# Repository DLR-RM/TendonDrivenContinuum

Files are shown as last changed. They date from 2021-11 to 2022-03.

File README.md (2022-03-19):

# Open Source Tendon-Driven Continuum Mechanism: A Platform for Common Research in Soft Robotics 

<p align="center">
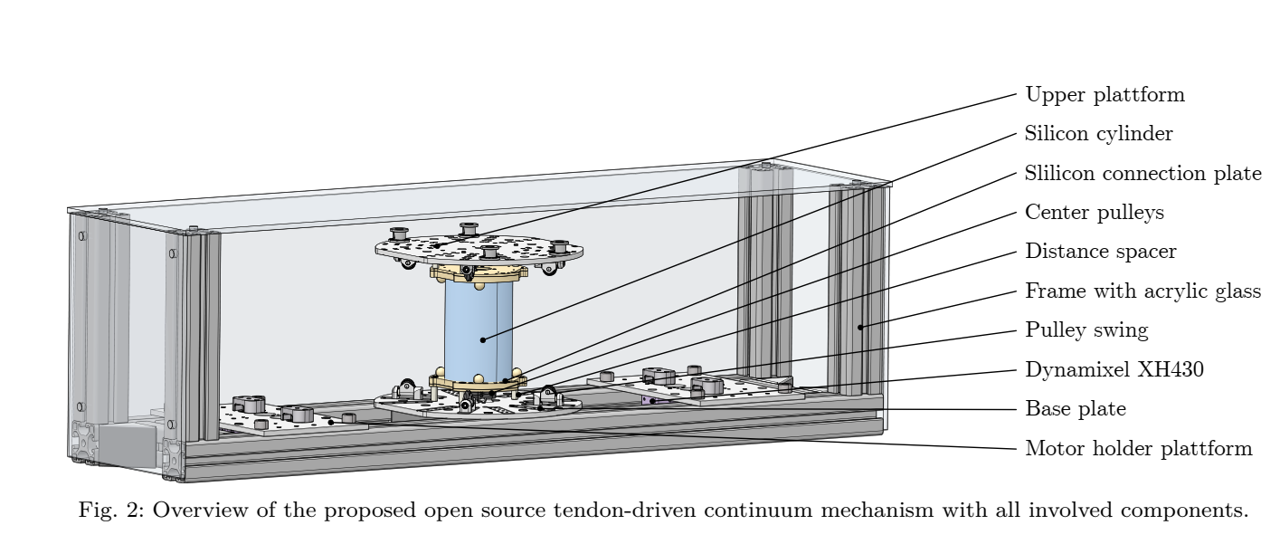
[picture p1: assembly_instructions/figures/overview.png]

</p>

This repository covers the CAD files (.stp) and assembly instruction to built a tendon-driven continuum mechanism research platform. If you want to built this system, please reference our corresponding publication [1].

## Abstract of the publication [1]
This paper introduces a tendon-driven continuum mechanism platform for research on design, modeling, state estimation, and control of this challenging robotic component envisioned as highly versatile and mechanically robust joint for future robotic systems. To propel the corresponding research areas, a common platform is presented for benchmarking and transferability of results, approaches, and designs among different research groups. The proposed mechanical design including all components is open source, whereas electronics and actuation are off-the-shelf. Research groups are enabled to build up their own system as all relevant CAD-files and assembly instructions are made accessible through GitHub. With that, a fundamental goal in research is achieved and will push continuum joints towards real application scenarios for future soft robots.

## Content of the repository

| Description | Link | Subfolder
| --- | --- | --- |
| Creo Design | [tdc_neck_asm.stp](https://github.com/DLR-RM/TendonDrivenContinuum/blob/main/CAD/tdc_neck_asm.stp) | [CAD](https://github.com/DLR-RM/TendonDrivenContinuum/tree/main/CAD) |
| Assembly Instructions |[Assembly Instructions Overview](https://github.com/DLR-RM/TendonDrivenContinuum/blob/main/assembly_instructions/assembly_instructions_overview.pdf).| [Assembly Instructions](https://github.com/DLR-RM/TendonDrivenContinuum/tree/main/assembly_instructions) |
| Control Interface | | 
| Readable Version | [deutschmann2022_robosoft_final_submission.pdf](https://github.com/DLR-RM/TendonDrivenContinuum/blob/main/paper/deutschmann2022_robosoft_final_submission.pdf) |[paper](https://github.com/DLR-RM/TendonDrivenContinuum/tree/main/paper) |

[1] Deutschmann, Bastian, Reinecke, Jens, Dietrich, Alexander: "Open Source Tendon-driven Continuum Mechanism: A common Platform for Research in Soft Robotics" accepted for publication in: IEEE International Conference on Soft Robotics (Robosoft), 2022.

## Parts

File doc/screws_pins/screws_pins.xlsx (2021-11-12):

Screws:
Type | diameter [mm] | length [mm] | amount | factor of testbed | Total | for which junction?
Cylinderhead | M3 | 8 | 4 | 2 | 8 | BPOM to BPOU
Cylinderhead | M2 | 6 | 6 | 2 | 12 | BPOO to BPOU
Cylinderhead | M4 | 25 | 3 | 2 | 6 | interface plate through distance spacer to lower/upper platform
Cylinderhead | M2 | 4 (8) | 4 | n_t*2 | n_t*8 | pulley swing to lower/upper platform (pulley swing through distance plate to lower/upper platform)
Cylinderhead | M3 | 8 | 6 | 1 | 6 | one side of the silicon mold to the other
Cylinderhead | M3 | 12 | 12 | 1 | 6 | connet assembled mold to interface upper/lower plates
Cylinderhead | M2 | 6 | 1 | n_t | n_t | connect Dynamixel interface plate with Dynamixel
Cylinderhead | M2.5 | 12 | 4 | n_t | n_t*4 | connect Dynamixel with motor holder plate
Cylinderhead | M2 | 4 | 4 | n_t | n_t*4 | connect Dynamixel interface plate with winch
Dowel pins:
Type | diameter | length | amount | factor of testbed | Total | for which junction?
H | 4 | 8 | 2 | 2 | 4 | BPOO to BPOU
H | 4 | 7 | 1 | n_t*2 | n_t*2 | pulley to swing

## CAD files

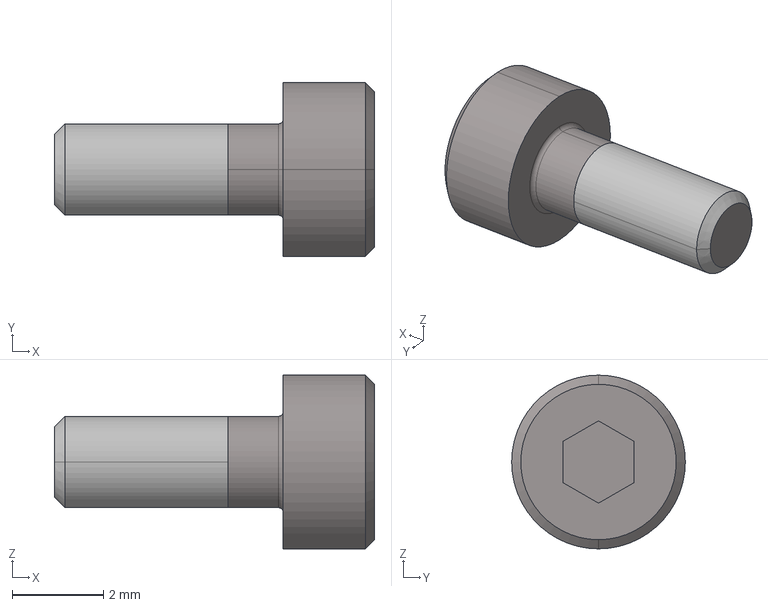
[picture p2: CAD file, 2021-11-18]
CAD/sc_d912_m02x05_af44_prt.stp
7.00 x 3.80 x 3.80 mm

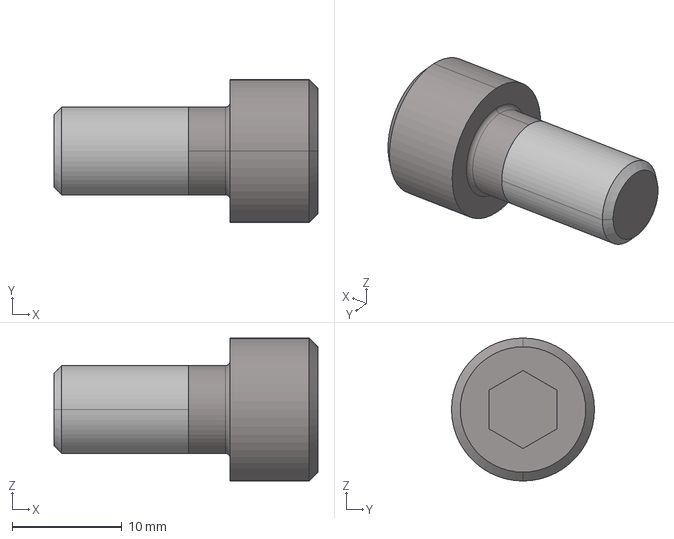
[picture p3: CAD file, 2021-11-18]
CAD/sc_d912_m08x16_prt.stp
24.0 x 13.0 x 13.0 mm

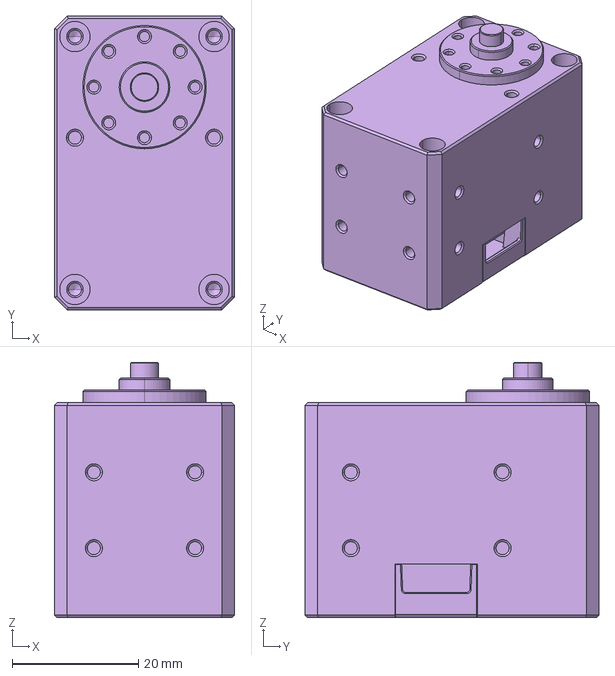
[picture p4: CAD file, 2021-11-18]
CAD/x-430_idle_prt.stp
28.5 x 46.5 x 40.4 mm

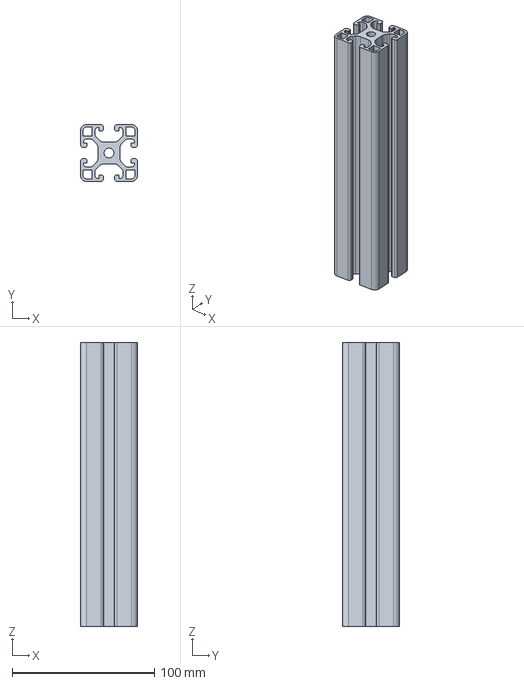
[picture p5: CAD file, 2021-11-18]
CAD/kt_item8_40x40_l_af26_prt.stp
40.0 x 40.0 x 200.0 mm

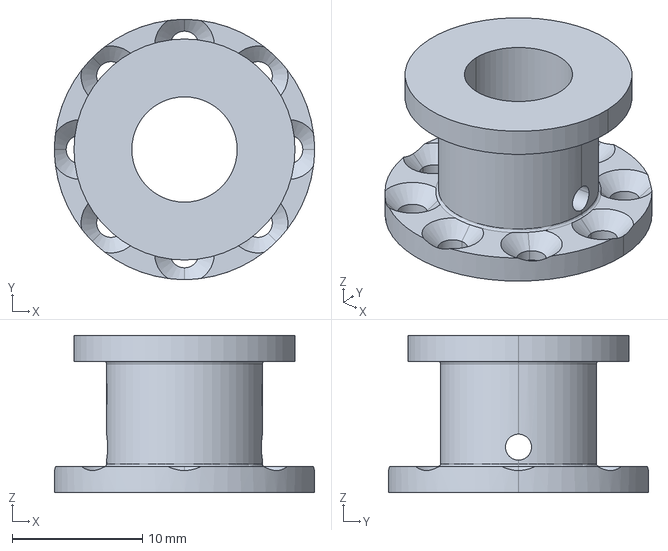
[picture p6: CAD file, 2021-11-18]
CAD/tdc_simpl_elast_winch_prt.stp
20.0 x 20.0 x 12.1 mm

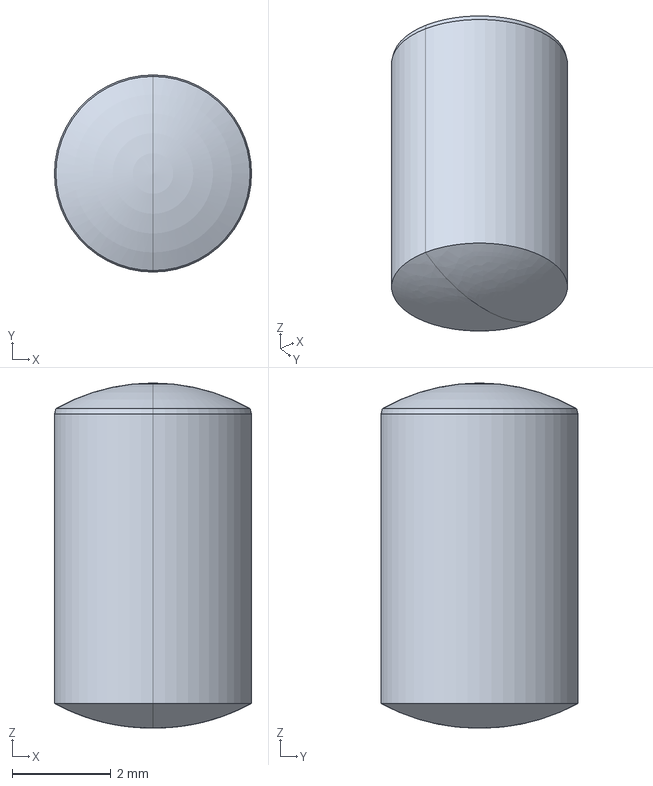
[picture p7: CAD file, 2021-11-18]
CAD/ps_d6325_04x07_prt.stp
4.00 x 4.00 x 7.00 mm

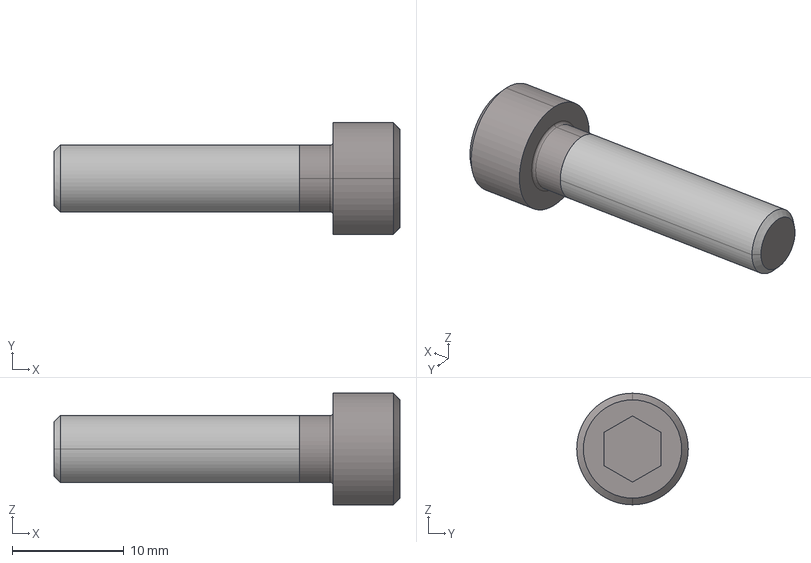
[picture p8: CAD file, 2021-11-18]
CAD/sc_d912_m06x25_af9_prt.stp
31.0 x 10.0 x 10.0 mm

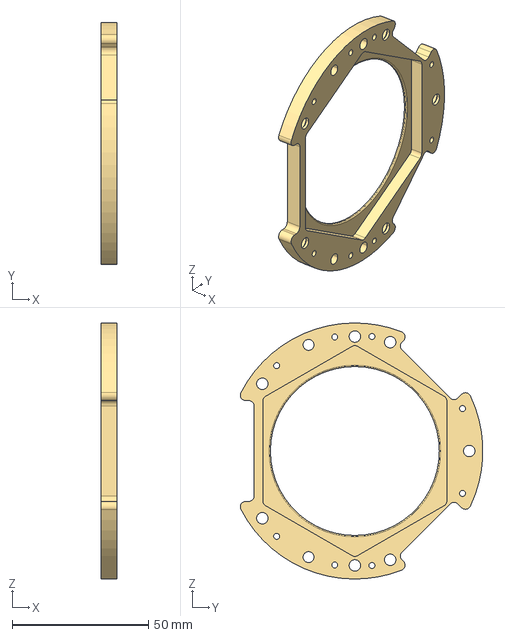
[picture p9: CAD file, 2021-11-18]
CAD/tdc_neck_bpoo_prt.stp
5.70 x 89.0 x 94.0 mm

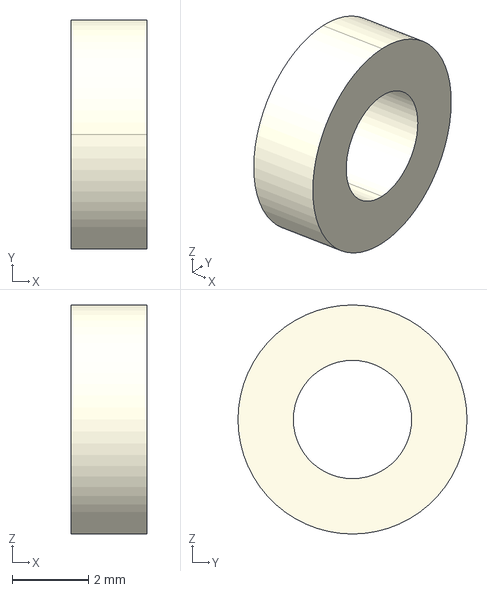
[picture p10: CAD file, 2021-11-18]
CAD/kt_distanzhuelse_03-06_af20_prt.stp
2.00 x 6.00 x 6.00 mm

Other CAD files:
CAD/sc_d912_m02x05_af45_prt.stp
CAD/sc_d912_m02x05_af49_prt.stp
CAD/sc_d912_m02x05_af53_prt.stp
CAD/sc_d912_m02x05_af42_prt.stp
CAD/sc_d912_m02x05_af46_prt.stp
CAD/sc_d912_m02x05_af38_prt.stp
CAD/sc_d912_m02x05_af63_prt.stp
CAD/sc_d912_m02x05_af43_prt.stp
CAD/sc_d912_m02x05_af37_prt.stp
CAD/kt_distanzhuelse_03-06_af17_prt.stp
CAD/kt_distanzhuelse_03-06_af18_prt.stp
CAD/kt_distanzhuelse_03-06_af19_prt.stp
CAD/kt_distanzhuelse_03-06_af21_prt.stp
CAD/kt_distanzhuelse_03-06_af22_prt.stp
CAD/kt_distanzhuelse_03-06_af23_prt.stp
CAD/kt_distanzhuelse_03-06_af24_prt.stp
CAD/kt_distanzhuelse_04-06_af12_prt.stp
CAD/kt_distanzhuelse_04-06_af13_prt.stp
CAD/kt_distanzhuelse_04-06_af14_prt.stp
CAD/kt_distanzhuelse_04-06_af15_prt.stp
CAD/kt_distanzhuelse_04-06_af16_prt.stp
CAD/kt_distanzhuelse_04-06_af17_prt.stp
CAD/kt_item8_40x40_l_af18_prt.stp
CAD/kt_item8_40x40_l_af19_prt.stp
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

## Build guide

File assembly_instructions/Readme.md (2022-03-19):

# Content 
The order of assembly is detailed in [Assembly Instructions Overview](https://github.com/DLR-RM/TendonDrivenContinuum/blob/main/assembly_instructions/assembly_instructions_overview.pdf).

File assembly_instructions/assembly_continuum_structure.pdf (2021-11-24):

## Assembly instructions: continuum structure

Bastian Deutschmann, Jens Reinecke and Alexander Dietrich

{Bastian.Deutschmann, Jens.Reinecke, Alexander.Dietrich}@dlr.de

DLR.de • slide 1

## Overview testbed

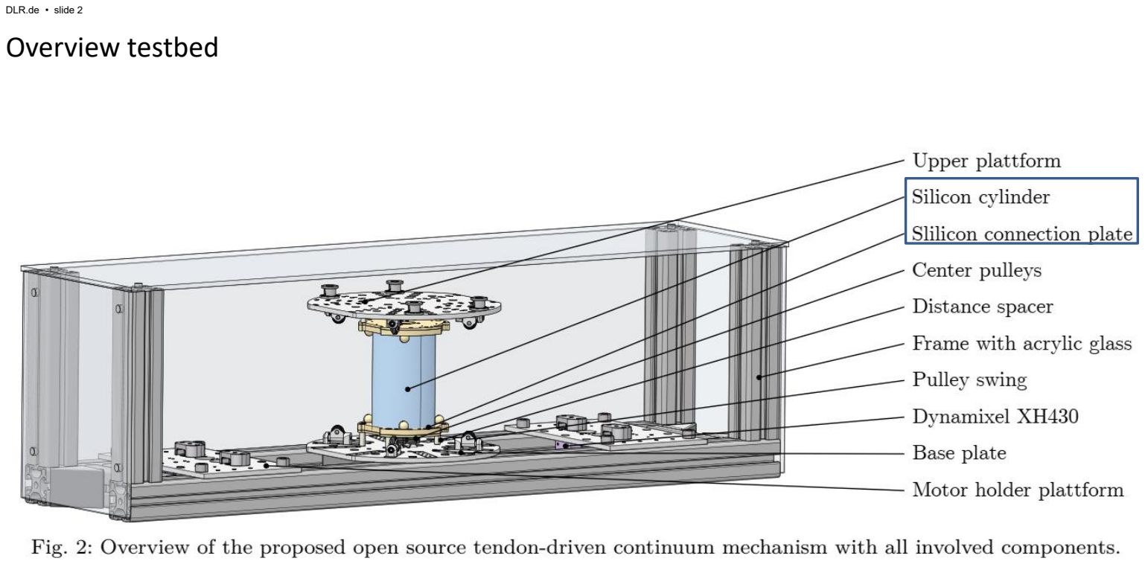
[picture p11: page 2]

## Overview of the contiuum structure

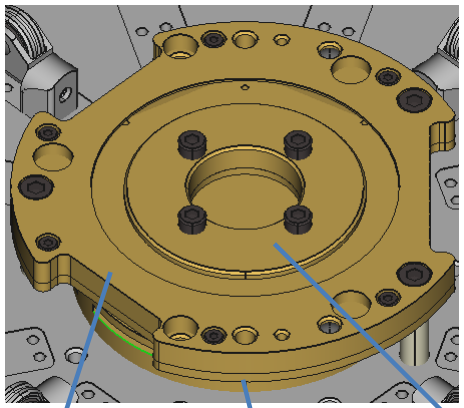
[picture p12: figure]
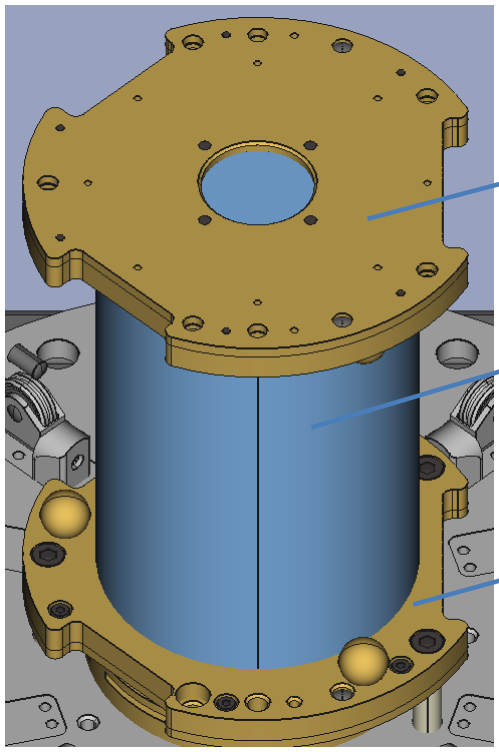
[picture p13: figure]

Upper interface plate

Lower interface plate

Continuum structure

TDC_NECK_BPOU

TDC_NECK_BPOO | TDC_NECK_BPOM

## Continuum structure components

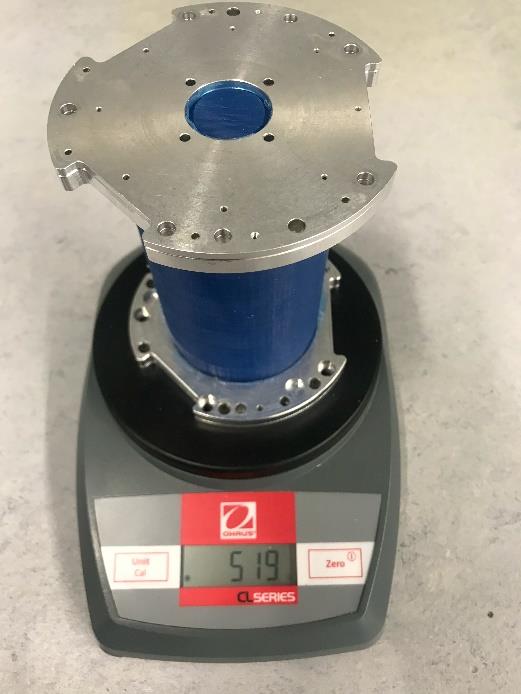
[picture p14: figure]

Manufacturing parts:
- Interface plate (3 parts)
- Lower part interface plate (TDC_NECK_BPOU)
- upper part interface plate (TDC_NECK_BPOO)
- Middle part interface plate (TDC_NECK_BPOM)
- Molds (3D-printed)
- Funnel (3D-printed)

Off-the-shelf parts:
- 2x2x dowel pin h6 ø4x8
- 2x6x Cylinderhead screw M2x6
- 2x4x Cylinderhead screw M3x8
- 6x Cylinderhead screw M3x8mm
- Silicon (e.g. Dragon skin shore 30A)
- Release Agent

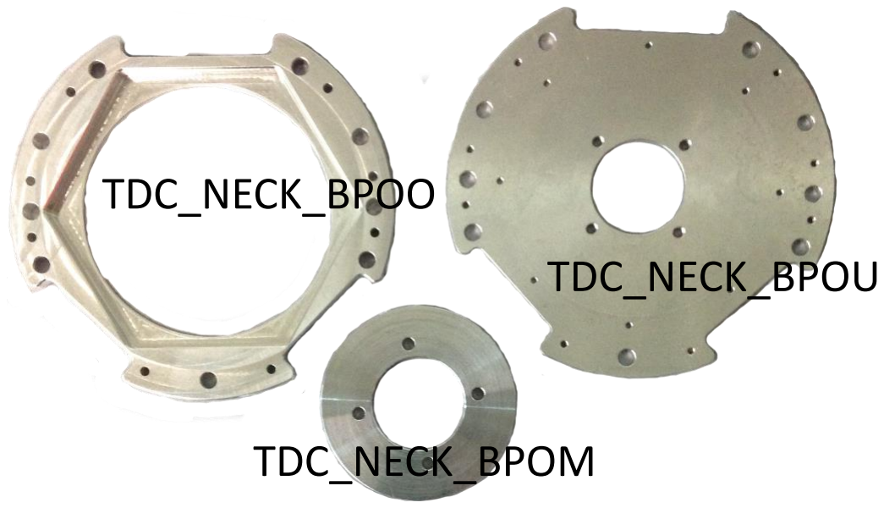
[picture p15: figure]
TDC_NECK_BPOU; TDC_NECK_BPOO; TDC_NECK_BPOM

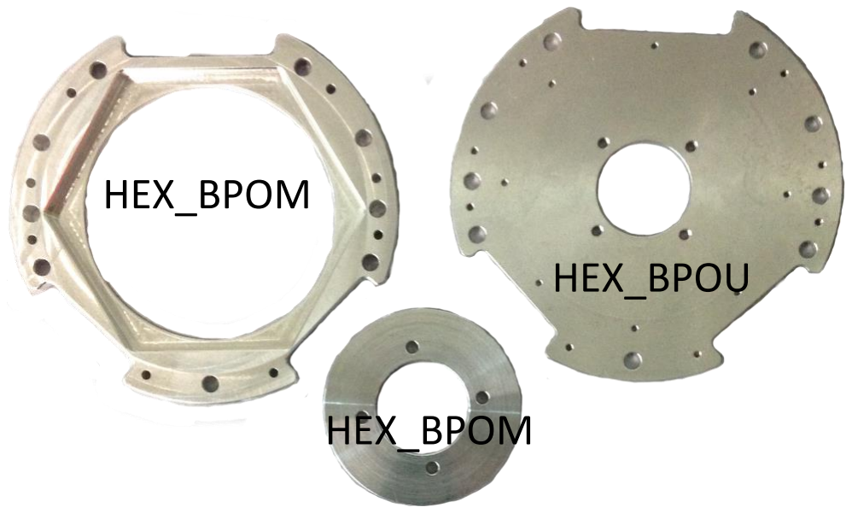
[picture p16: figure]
HEX_BPOU; HEX_BPOM

## Assembly interface plate

Tools:
- Allenkey
- Parallel plyers

Instructions:
- Clean all parts using iso-propanol
- Pair HEX_BPOO and HEX_BPOU by the dowel pins using the parallel plyers
- Pair HEX_BPOO and HEX_BPOU with 6x M2x6 using an allenkey
- Pair HEX_BPOU and HEX_BPOM with 4x M3x8 using an allenkey
- Repeat all steps for 2nd interface plate

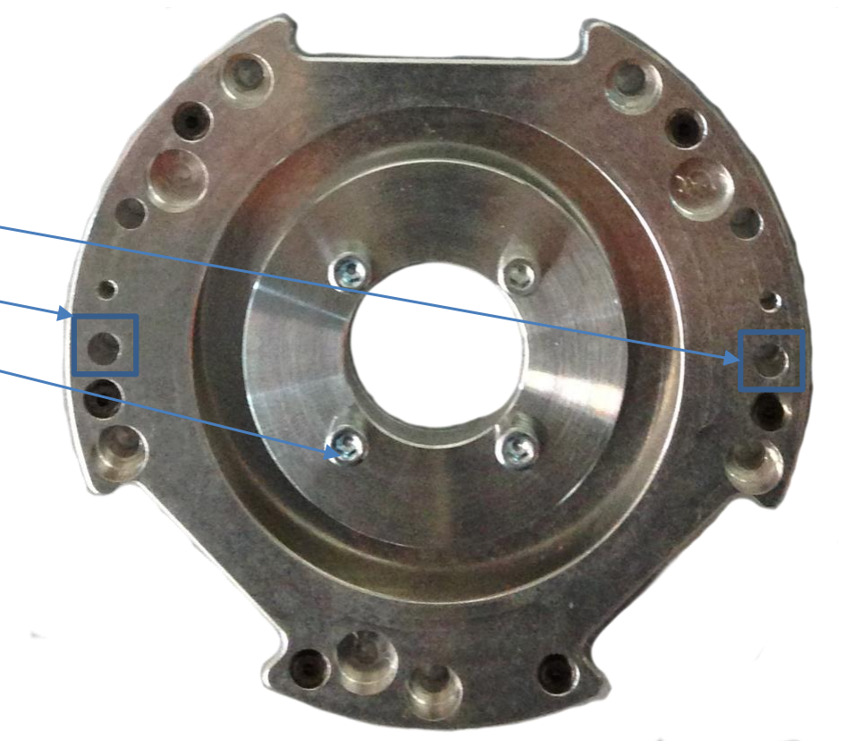
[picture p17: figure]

## Assembly of interface plate and moldings

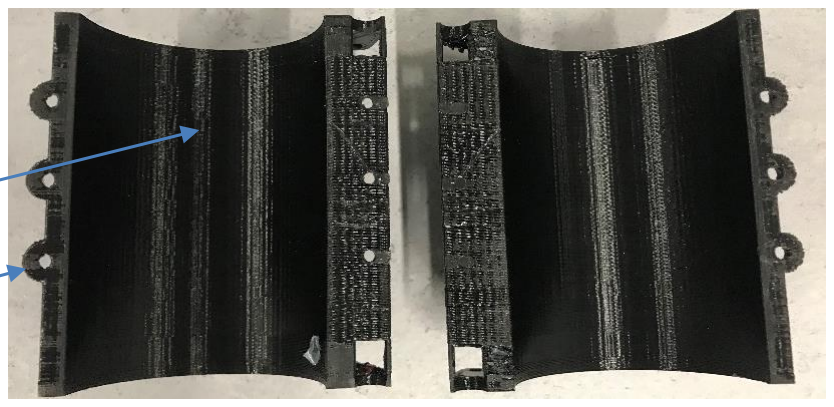
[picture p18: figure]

Tools:
- Allenkey

Instructions:
- Cover the inside of the molds with the release agent
- Pair the two molds with each other using 6x M3x8 and corresponding nuts
- Pair the molds and the lower and upper interface plate using screws 2x6x M2x12

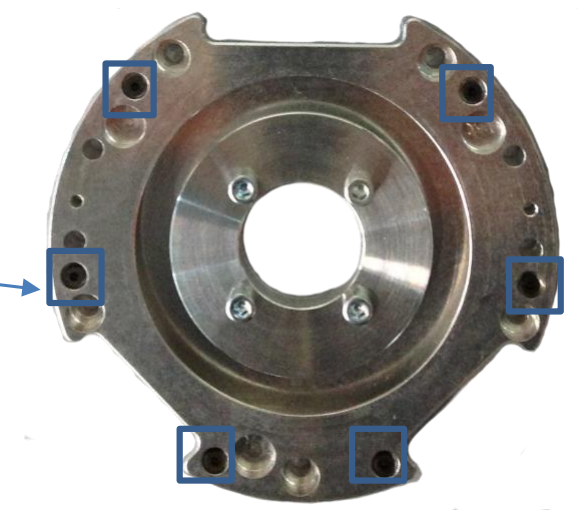
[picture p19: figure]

## Instructions for moldings

Tools
- Vacuum pump
- Container for to mix 2-component silicon & Stirring staff
- Digital scale

Parts:
- Assembled interface plates with moldings
- 3D-printed Funnel

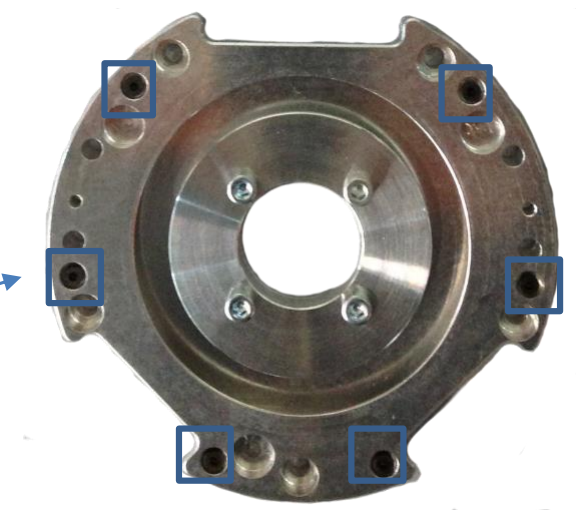
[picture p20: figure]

Instructions
- Mix 2 component silicon in container at the correct ratio (using the scale) with the stirring staff.
- Evacuate the mixture by a vacuum pump to remove air-bubbles with the mixture
- Pure the evacuated mixture into the assembled moldings using the funnel
- Let it cure for the respective time (24h for dragon skin)
- Remove the molds
- Pair HEX_BPOO and HEX_BPOU with 2x 6x M2x6 using an allenkey

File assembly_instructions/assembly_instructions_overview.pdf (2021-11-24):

## Assembly instructions: overview

Bastian Deutschmann, Jens Reinecke and Alexander Dietrich

{Bastian.Deutschmann, Jens.Reinecke, Alexander.Dietrich}@dlr.de

DLR.de • slide 1

## Overview testbed

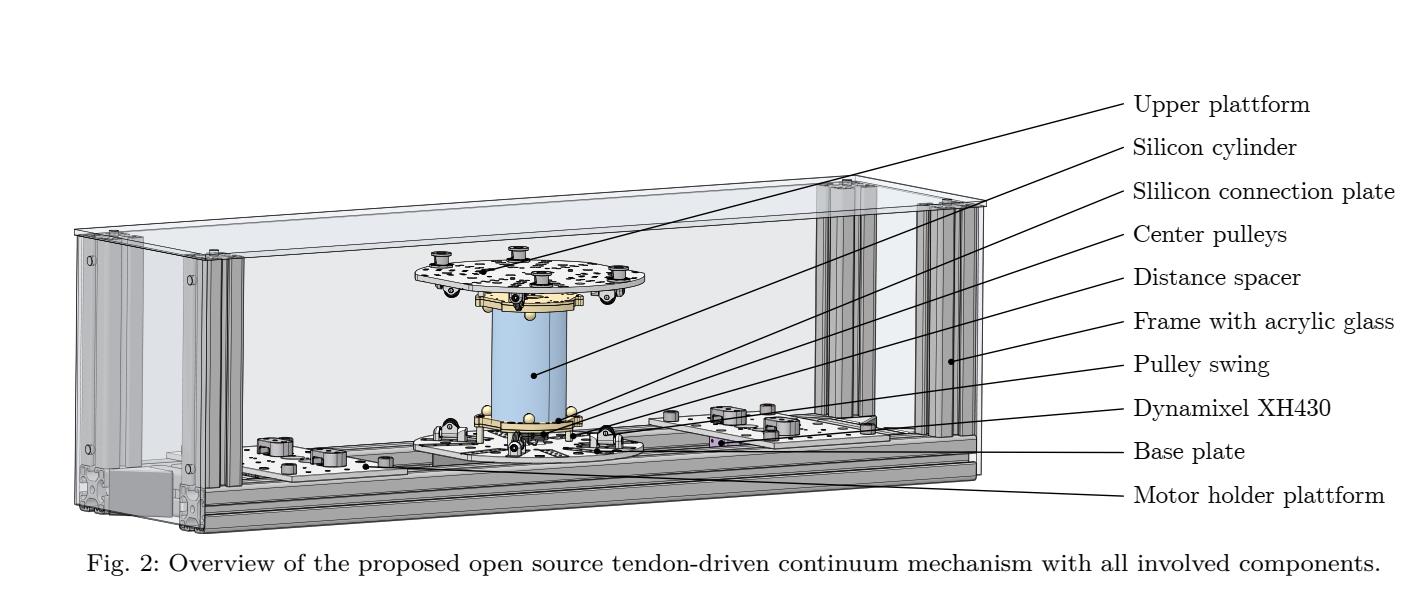
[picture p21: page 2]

## Assembly instructions: overview

In order to assemble the open source testbed, the following order of assembly is suggested:

1) Assembly of pulley swing
2) Assembly of continuum structure (Silicon cylinder)
3) Assembly of continuum and platform
4) Assembly of tendons
5) Assembly of motor holder platform

In order to perform each of the five steps, please refer to the corresponding assembly instruction .pdf file

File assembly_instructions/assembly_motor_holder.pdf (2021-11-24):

## Assembly instructions: motor holder

Bastian Deutschmann, Jens Reinecke and Alexander Dietrich

{Bastian.Deutschmann, Jens.Reinecke, Alexander.Dietrich}@dlr.de

DLR.de • slide 1

## Overview testbed

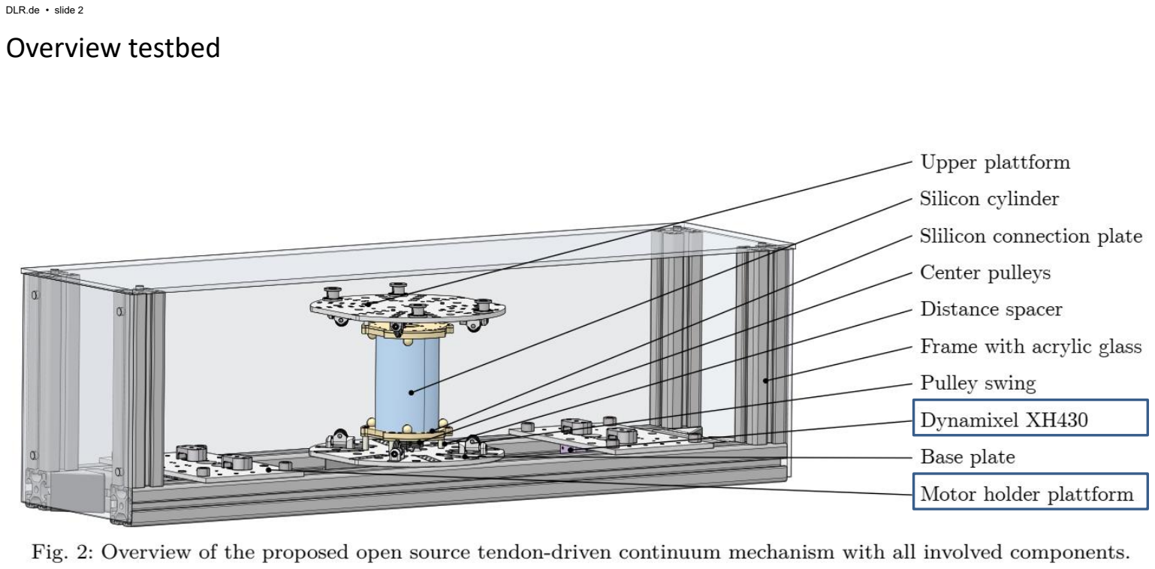
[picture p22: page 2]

## Overview of motor holder

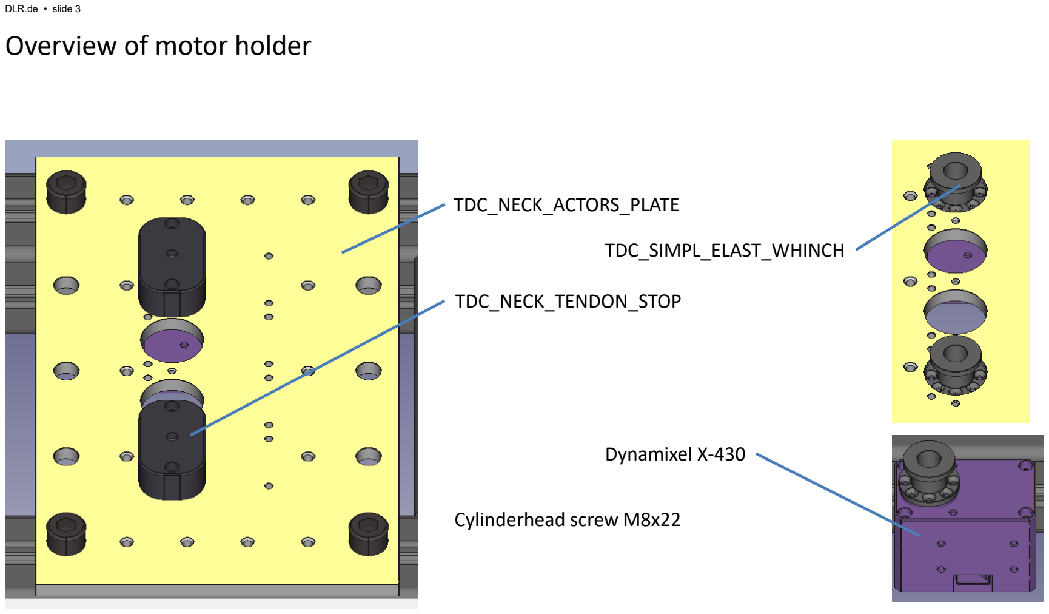
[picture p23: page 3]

TDC_NECK_ACTORS_PLATE

TDC_NECK_TENDON_STOP

Cylinderhead screw M8x22

TDC_SIMPL_ELAST_WHINCH

Dynamixel X-430

## Components

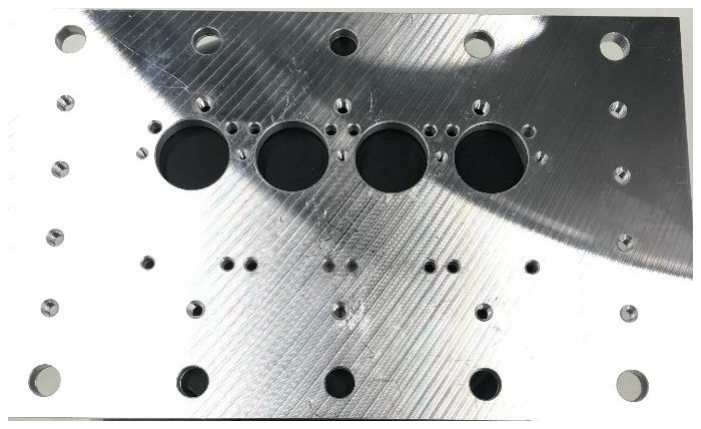
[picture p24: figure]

Manufacturing parts
- 2x motor holder plater (TDC_NECK_ACTORS_PLATE )
- n_t tendon winches (TDC_SIMPL_ELAST_WINCH)
- N_t Tendon stops (TDC_NECK_TENDON_STOP)

Off-the-shelf parts:
- n_t Dynamixel motors with interface plate
- 4xn_tx M2.5x12 (mount Dynamixel on holder)
- 4xn_tx M2x4 (mount winch on Dynamixel interface plate)
- n_tx M2x6 (mount interface plate on Dynamixel output shaft

Tools:
- Allenkey

## Assembly instructions: motor holder

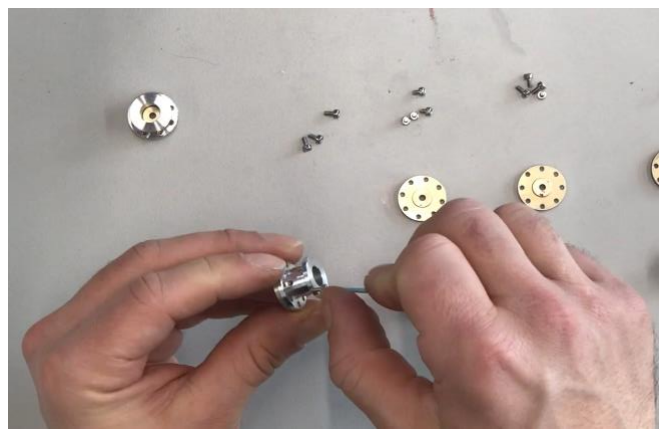
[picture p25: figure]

Instructions:
- Mount each of the n_t winches onto the Dynamixel interface plate using 4xM2x4 cylinderhead screws
- Connect each Dynamixel interface plate with the output shaft of a dynamixel motor using M2x6 cylinderhead screw
- Mount each of the n_t dynamixel motor with 4xM2.5x12 cylinderhead screw to the actuator plate
- Mount each of the n_t tendon stops onto the motor holder plate

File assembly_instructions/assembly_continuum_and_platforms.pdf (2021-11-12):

## Assembly instructions: continuum structure and the platforms

Bastian Deutschmann, Jens Reinecke and Alexander Dietrich

{Bastian.Deutschmann, Jens.Reinecke, Alexander.Dietrich}@dlr.de

DLR.de • slide 1

## Overview testbed

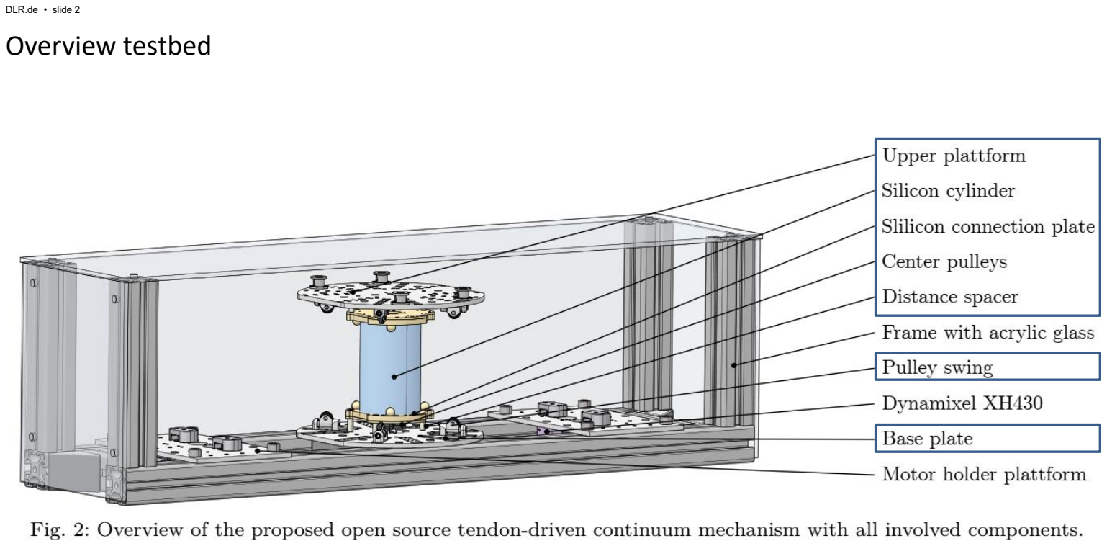
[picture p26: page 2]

## Components

Assembled parts
- Continuum structure with
- 8x Pulley
- 2*n_t pulley swings

(n_t = number of tendons)

Manufacturing parts
- 2x DV_NECK_DFG_BASE_PLATE (Upper/lower platform)
- n_t x DV_NECK_ADAPT_UML (Distance spacer to adjust hight of pulley swing)

Off-the-shelf parts:
- Distance spacer (of length l)
- 6x Screws (fixing continuum and platform)

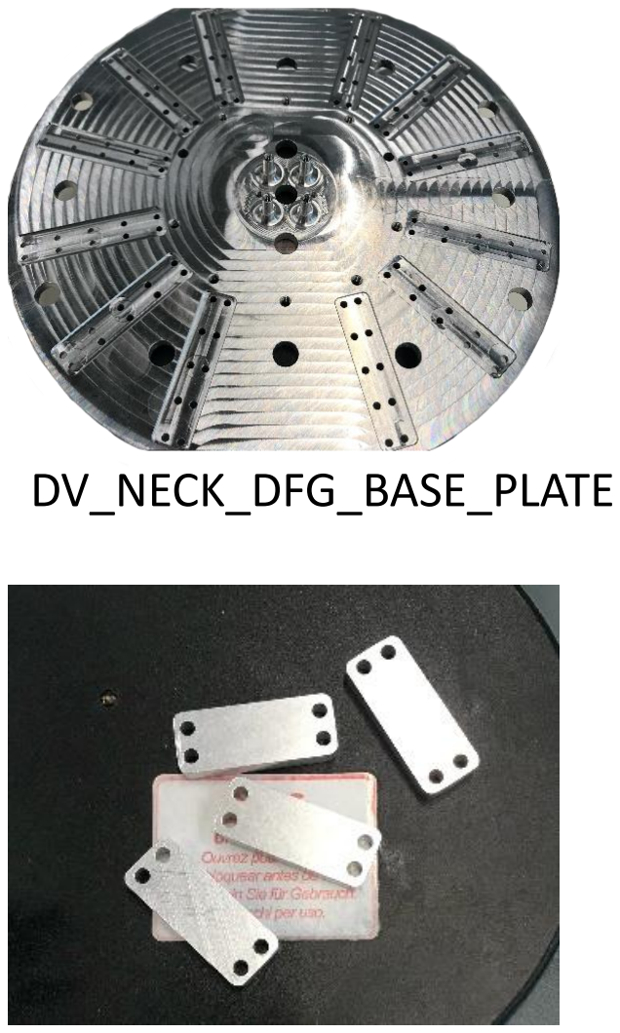
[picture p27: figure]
DV_NECK_DFG_BASE_PLATE

DV_NECK_ADAPT_UML

## Assembly instructions: lower platform with central pulleys

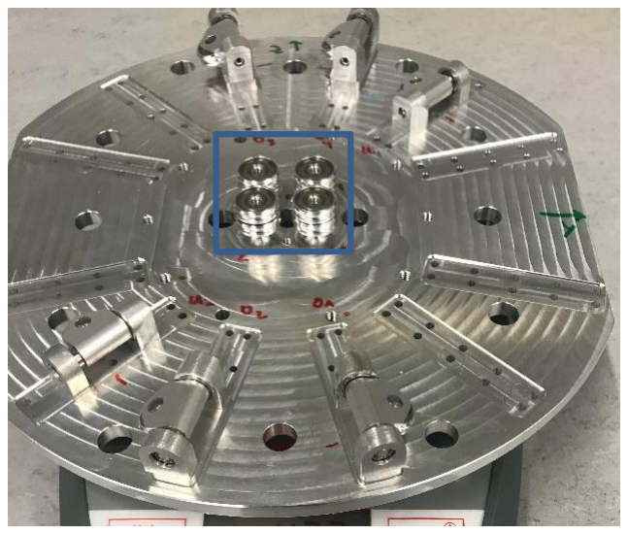
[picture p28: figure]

Tools:
- Allenkey
- Different washers or other spacers

Instructions:
- 8x pulleys are to be assembled to the center of the lower platform at four mounting spots (2 pulley on top of each other respectively)
- The inner diameter of the pulley bearing and the repsective mounting at the lower platform represent a fitting, therefore need to be assembled with special care
- Use a screw (spec?) + additional spacers/washers to slowly push the bearing on the inner diameter on the mounting spot
- Repeat the procedure 7x

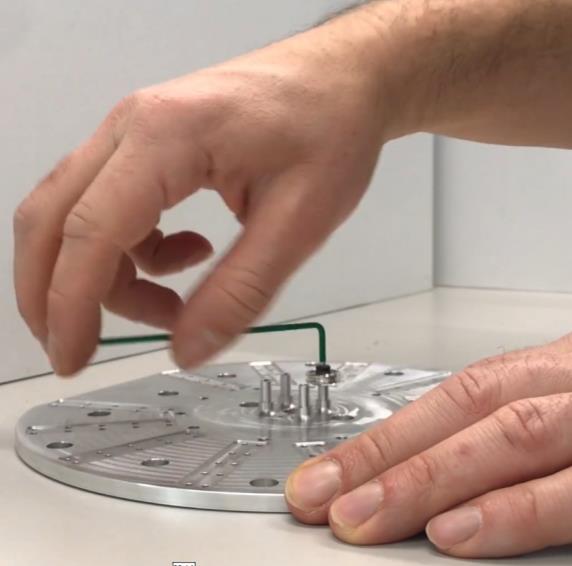
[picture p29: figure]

## Assembly instructions: lower/upper platform with pulley swings

Tools:
- Allenkey

Instructions:
- Decide on the number of tendons
- Decide, which tendon is routed on the lower or upper central pulley
- Dependent on which central pulley is used for the routing, distance spacer (DV_NECK_ADAPT_UML) need be put below the pulley swing
- Assemble pulley swing (+ additional spacer) with 4 Zylinderkopfschrauben (spec? (spec for with spacer))

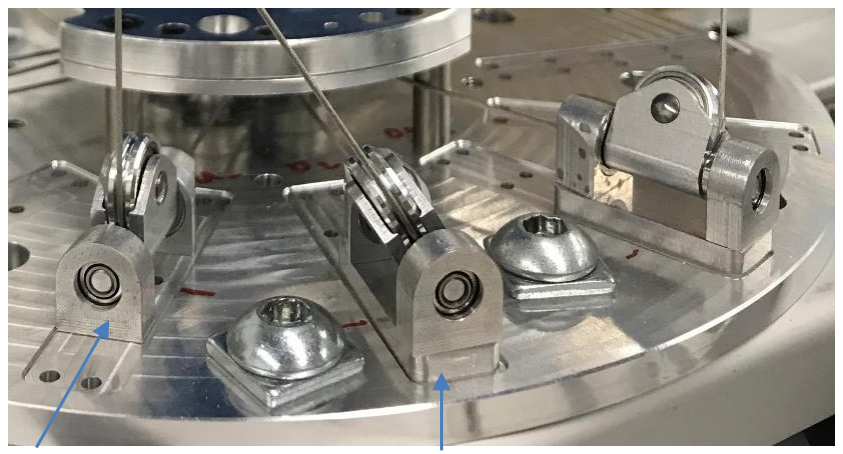
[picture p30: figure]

no spacer | spacer used

## Assembly instructions: lower/upper platforms and continuum structure

Tools
- Allenkey

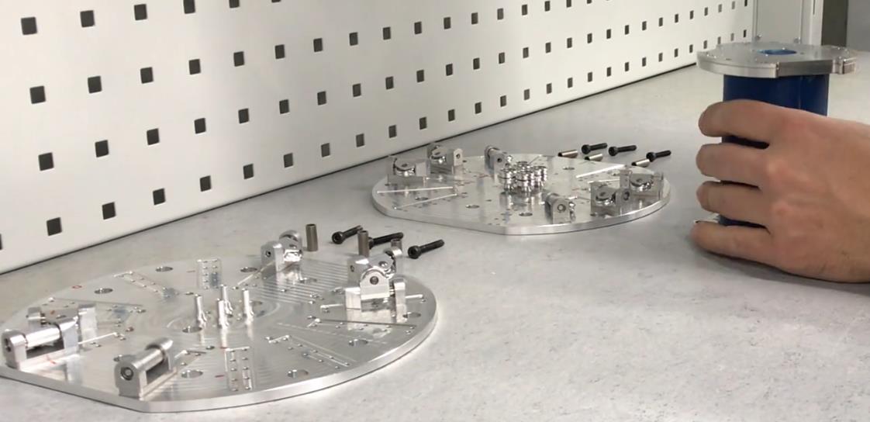
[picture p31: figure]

Instructions:
- Decide on the used distance spacer and select the three screws for the lower platform (and the three screws for the upper platform respectively)
- Place the distance spacer in between the continuum structure and the platform.
- Use one screw (spec?) after the other to fix the continuum structure through the spacer on the platform using the allenkey

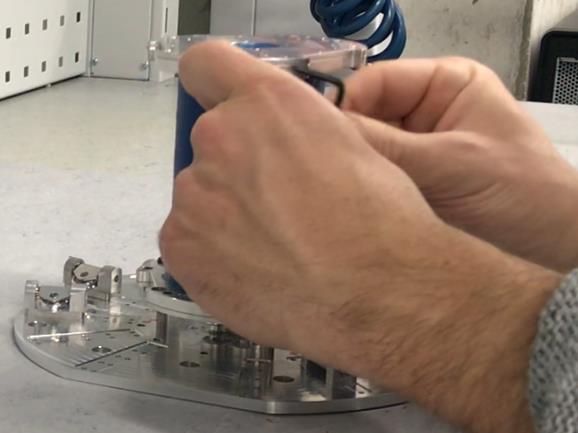
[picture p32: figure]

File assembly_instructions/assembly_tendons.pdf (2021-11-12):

## Assembly instructions: tendons

Bastian Deutschmann, Jens Reinecke and Alexander Dietrich

{Bastian.Deutschmann, Jens.Reinecke, Alexander.Dietrich}@dlr.de

DLR.de • slide 1

## Overview testbed


## Components

Assumption: steal tendons are used

Assembled parts
- Continuum mechanism with pulley swings

Manufacturing parts
- n_t x tendon whinch
- Tendons (e.g. steal or dynamixel)

Off-the-shelf parts:
- n_t x screw (M6 x lenght?) and corresponding nut (M6)
- Ferrul to crimp

Tools:
- Crimp plyers
- Tendon cutting plyers
- Allenkey
- 10mm spanner

## Assembly instructions: routing of tendons in pulley swing

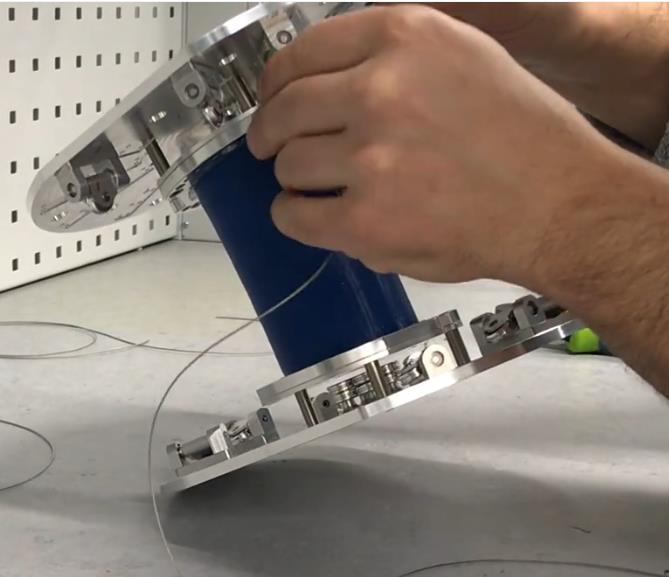
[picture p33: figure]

Tools:
- Cutting plyers
- Tape measure

Instructions:
- Cut n_t tendons to predefined length (how to do it?)
- Input tendon from the outside into the upper and the lower pulley swing for every tendon
- Route the tendon through the upper platform by one of the holes

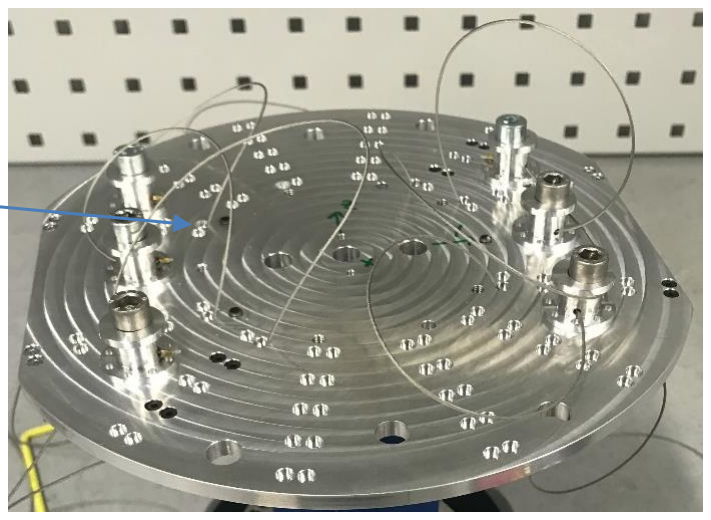
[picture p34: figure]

## Assembly instructions: termination of tendons in upper platform

Tools:
- Allenkey
- Crimp plyers
- Crimps (Ferules)

Instructions:
- Route the upper end of a tendon through the middle of a whinch using the small holes
- Crimp the tendon on the outer side with a ferule using the crimp plyers
- Mount the whinch with the tendon onto the upper platform using the M6x(length) screw and the corresponding nut.

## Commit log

2021-11-17 add: inital commit of CAD files (.stp) and CAD assembly
    [kt_distanzhuelse_03-06_af10_prt.stp, kt_distanzhuelse_03-06_af11_prt.stp, kt_distanzhuelse_03-06_af12_prt.stp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]
2021-11-18 removed outdated .stl files and assembly
    [kt_distanzhuelse_03-06_af10_prt.stp, kt_distanzhuelse_03-06_af11_prt.stp, kt_distanzhuelse_03-06_af12_prt.stp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]
2021-11-18 added CAD files + asm file
    [kt_distanzhuelse_03-06_af17_prt.stp, kt_distanzhuelse_03-06_af18_prt.stp, kt_distanzhuelse_03-06_af19_prt.stp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]
2021-11-24 add: reworked assembly instructions
2022-03-19 add: .md file for assembly instructions
